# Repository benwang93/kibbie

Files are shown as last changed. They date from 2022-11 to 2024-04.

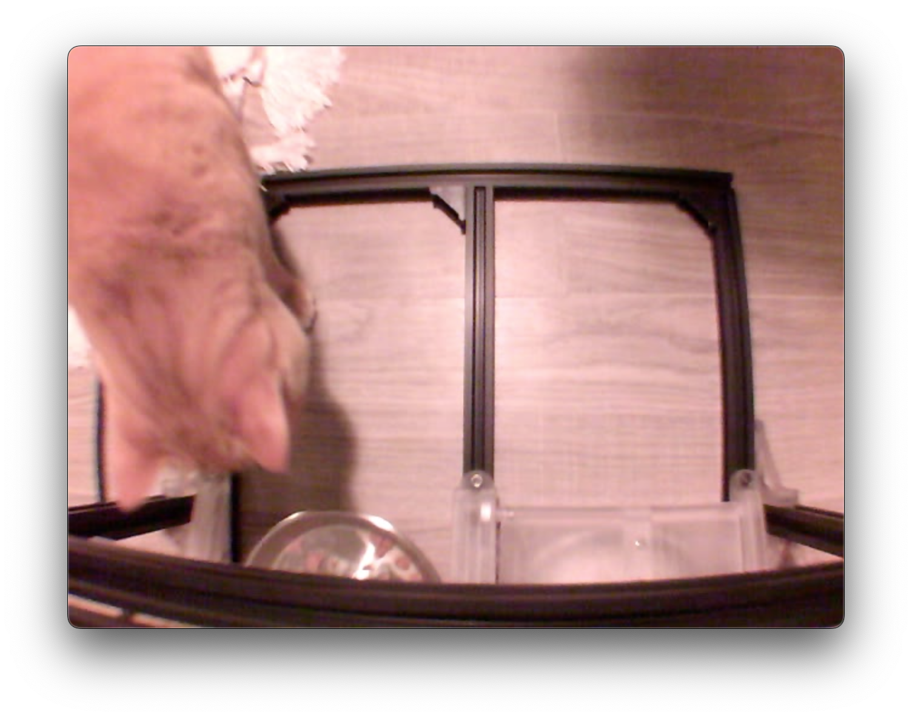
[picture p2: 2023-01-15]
software/images/cami-gray_background.png

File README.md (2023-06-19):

# Project Kibbie

Automated kibble dispenser

## Setup

### Raspberry Pi (embedded)

Hardware requirements:

- Raspberry Pi 3 B+
- 64 GB MicroSD card with Raspbian (see https://www.raspberrypi.com/software/ for installation instructions)

Instructions:

1. On Raspberry Pi with Raspian, clone this repo to `/home/<username>/`
2. Increase swap size from 100MB to something big (2048MB?). See https://peppe8o.com/set-raspberry-pi-swap-memory/
3. Install required python packages by running `setup_raspberrypi.sh`
4. Enable I2C on Pi via the Pi configuration tool. For more information, see https://learn.adafruit.com/adafruits-raspberry-pi-lesson-4-gpio-setup/configuring-i2c
5. Set up kibbie's run.sh to run on startup

Additionally, set up SSH and VNC on the Pi.

#### Python package setup

To install OpenCV on Raspberry Pi 3 Model B+, followed these instructions: https://raspberrypi-guide.github.io/programming/install-opencv and installed it in a virtualenv. Note that these are part of the `setup_raspberrypi.sh` script.

```
. venv/bin/activate

sudo apt-get install build-essential cmake pkg-config libjpeg-dev libtiff5-dev libjasper-dev libpng-dev libavcodec-dev libavformat-dev libswscale-dev libv4l-dev libxvidcore-dev libx264-dev libfontconfig1-dev libcairo2-dev libgdk-pixbuf2.0-dev libpango1.0-dev libgtk2.0-dev libgtk-3-dev libatlas-base-dev gfortran libhdf5-dev libhdf5-serial-dev libhdf5-103 python3-pyqt5 python3-dev -y

pip install opencv-python==4.5.3.56
```

#### Configuring swap memory

Copied from https://peppe8o.com/set-raspberry-pi-swap-memory/ (and tweaked the memory requirement to 2 GB)

Disable swap:

```
sudo dphys-swapfile swapoff
```

Change swap size in dphys-swapfile. Open this file for editing:

```
sudo nano /etc/dphys-swapfile
```

Identify CONF_SWAPSIZE parameter and change according to your needs. For example, I will change it to:

```
CONF_SWAPSIZE=2048
```

Exit and save. Enable swap and restart dphys service:

```
sudo dphys-swapfile swapon
sudo systemctl restart dphys-swapfile.service
```

Check that swap has changed value:

```
pi@raspberrypi:~ $ free
               total        used        free      shared  buff/cache   available
 Mem:         374964       36648      223092        2708      115224      282916
 Swap:        511996           0      511996
```

This will persist also after Raspberry PI reboot.

#### Configuring for run on startup

Source: https://stackoverflow.com/questions/12973777/how-to-run-a-shell-script-at-startup

Set up chrontab for kibbie:

```
$ crontab -e
@reboot  /home/<username>/kibbie/run.sh
```

### PC (development)

Run `setup_desktop.sh` to set up virtualenv and install development packages.

To ignore the `HardwareParameters.py` file, run:

```
git update-index --assume-unchanged software\lib\HardwareParameters.py
```

To start tracking again:

```
git update-index --no-assume-unchanged software\lib\HardwareParameters.py
```

Source: https://stackoverflow.com/questions/23673174/how-to-ignore-new-changes-to-a-tracked-file-with-git

### Software

#### FreeCAD

Design done with FreeCAD 0.20.1. Required modules:

- Assembly 3

##### Assembly 3 installation

1. Tools > Addon Manager
2. Search for and install Assembly 3
3. After restarting FreeCAD, load something that uses Assembly 3 (or select it from the menu, maybe create a new assembly?)
4. Will prompt you to install `py-slvs`. The install will appear to fail, but this is due to pip saying it needs to be upgraded. You're OK to dismiss the repeated prompts to install at this point.
5. Click on an assembly in the Model pane on the left, make sure that the assembly's "Solver Type" is set to "SolveSpace" in the left-hand "Property" pane.

# Feeder servo demo

See the `servo_demo` folder. Parts needed:

- `hardware\prints\servo_mount_plate\servo_mount_plate.ctb`
- `hardware\prints\servo_coupler_v1\Servo_coupler_v1.ctb`

Run script `servo_demo\kibbie_dispenser_demo.py`

## Other info

- [MakerFocus PWM Servo Motor Driver IIC Module 16 Channel PWM Outputs 12 Bit Resolution I2C Compatible with Raspberry Pi 4 3B+ 3B Zero/Zero W/Zero WH and Jetson Nano on Amazon](https://www.amazon.com/gp/product/B07H9ZTWNC)
- [Adafruit I2C configuration guide](https://learn.adafruit.com/adafruits-raspberry-pi-lesson-4-gpio-setup/configuring-i2c)
- [Adafruit Servo Hat instructions](https://learn.adafruit.com/adafruit-16-channel-pwm-servo-hat-for-raspberry-pi/attach-and-test-the-hat)

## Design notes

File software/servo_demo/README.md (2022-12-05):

# Servo demo

2 demos are contained here:
1. Demo from Waveshare (doesn't work very well and I had to change the python library from smbus to smbus2)
2. Adafruit library demo (works very well!)

Notes:
- Commanding angle changes faster than 100ms seems to cause the communication to be unstable and program crashes
- To run, install `adafruit-circuitpython-servokit` and then run `python3 adafruit_lib_test.py`

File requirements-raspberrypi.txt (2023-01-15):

opencv-python==4.5.3.56
adafruit-circuitpython-servokit
matplotlib

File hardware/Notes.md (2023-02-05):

# Design notes

## Servo coupler

### Servo horn

Hole pattern

- Diameter of horn is 20.6mm
- Screw holes
  - 12.80mm is closest between y-axis opposite screw holes
  - Each screw hole is 1.45-1.5mm diameter
  - Designing with 1.45mm for now (making it tighter)
- Distance from horn center to screw hole center on x/y axes must then be
    (12.80 / 2) + 1.45/2 mm = 7.125mm

- Closest measurement between the 2 outer holes in a 3-row is 5.4mm
- So the spacing between 2 holes should be: (5.4mm + 1.45) / 2 = 3.425mm

### D Shaft design & plate thickness

- D shaft is around 5.65mm from flat side of D to the opposite side of circle
  - D shaft diameter is 7.60mm

How long should the shaft be? How thick should base plate be?

- Servo:
  - From screw plate top to top of servo horn is ~16mm
- Hand turn
  - Chrome part sits flush with black plastic when fully inserted
  - Rod is around 64mm long
  - at 39mm from chrome handle, the taper happens on the D shaft

- So from servo horn face to end of rod should be around (64 - 16) = 50mm
- For v1, we can have the screws enter from the far side from the servo and then poke out of the servo horn at the servo side. This would require our base piece to be around 6.5 mm
  - Screw is 10mm long (excluding the tip, which adds around another 1 mm)

Base plate thickness: 6.5mm
Shaft length: 50mm - 6.5mm = 44.5mm

### D Shaft taper

- Last 25mm of shaft is tapered

## Kibbie Monitor Circuit Design

### Design requirements:
- P1: Monitor each dispenser's servo motor current (3 servos per corral, 2 corrals total)
- P1: Communicate overcurrent per-side to Raspberry Pi for shutting down bad side and falling back to single side operation
- P1: Ability to shut off servos on overcurrent. This might be doable via thee Raspberry Pi though?
- P1: Run off of 5V power from PSU
- P2: Watchdog via GPIO, where Raspberry Pi toggles a GPIO while Kibbie program is alive
- P2: Ability to cut power to Raspberry Pi if watchdog sees failure (5V relay, but to Kibbie)

### Components:
- USB A Breakout: https://www.sparkfun.com/products/12700
- Arduino Uno breadboard shield: https://www.sparkfun.com/products/13819
- Current sensor: https://www.sparkfun.com/products/12040
- Current sensor resistor:
  - 0.1 Ohm 5W 10 pcs: https://smile.amazon.com/HUABAN-10PCS-Watts-Metal-Resistor/dp/B08LW2THTJ

### Current monitoring:

#### Selecting R_S
Stall current of each servo is around 3A (https://smile.amazon.com/dp/B07MFK266B). 2 servos active at once (door + door lock) would be 6A.

From the Sparkfun hookup guide:

          V_OUT * 1kOhm
  I_S = ----------------
          R_S * R_L

To not consume too much power on the current sense resistor (so it's not terribly big), we could do:

P = I^2 * R

Let I = 6A. For a max power of 1.5W (so that we could use a 3W resistor), we would need around R = 1.5 W / 6A ^ 2 = 0.0417 Ohms. Can probably round up and use a **0.05 Ohm resistor, 3W**.

#### Selecting R_L

Next is to select a R_L. To get a reasonable voltage reading, let's say max current of 8A (which is what our power supply can do):

            I_S * 1kOhm
  V_OUT = ----------------
            R_S * R_L
            
            I_S * 1kOhm
  R_L = ----------------
            R_S * V_OUT

So at max current:

          8A * 1kOhm
  R_L = ---------------- = 32 kOhm, and a larger R_L would give a lower V_max. So we should be no less than 32 kOhm on R_L
          0.05Ohm * 5V

**Either 33k or 39k Ohm should work.**

#### Final voltages

Using:
            I_S * 1kOhm
  V_OUT = ----------------
            R_S * R_L

and R_S = 0.05 Ohm, R_L = 33 kOhm:

I_S   V_OUT         P_R (W)
0.1	  0.060606061	  0.0005
0.5	  0.303030303	  0.0125
1	    0.606060606	  0.05
1.5	  0.909090909	  0.1125
2	    1.212121212	  0.2
3	    1.818181818	  0.45
4	    2.424242424	  0.8
5	    3.03030303	  1.25
6	    3.636363636	  1.8
7	    4.242424242	  2.45
8	    4.848484848	  3.2

(See hardware/Electrical/Current_sense_calculations.xlsx)

### Reference:
- Current sensor hookup guide: https://learn.sparkfun.com/tutorials/ina169-breakout-board-hookup-guide

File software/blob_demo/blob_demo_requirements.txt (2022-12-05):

opencv-python
adafruit-circuitpython-servokit
matplotlib
scikit-image

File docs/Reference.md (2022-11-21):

Waveshare 16-channel servo driver documentation: https://www.waveshare.com/wiki/Servo_Driver_HAT
Adafruit guide and drivers: https://learn.adafruit.com/adafruit-16-channel-servo-driver-with-raspberry-pi/overview
RPi 3.5" LCD touchscreen documentation: https://www.waveshare.com/wiki/3.5inch_RPi_LCD_(A)

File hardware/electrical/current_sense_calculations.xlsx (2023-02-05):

R_S | 0.05 | Ohm
R_L | 33000 | Ohm
I_S | V_out | P_R
0.1 | 0.06060606061 | 0.0005
0.5 | 0.303030303 | 0.0125
1 | 0.6060606061 | 0.05
1.5 | 0.9090909091 | 0.1125
2 | 1.212121212 | 0.2
3 | 1.818181818 | 0.45
4 | 2.424242424 | 0.8
5 | 3.03030303 | 1.25
6 | 3.636363636 | 1.8
7 | 4.242424242 | 2.45
8 | 4.848484848 | 3.2

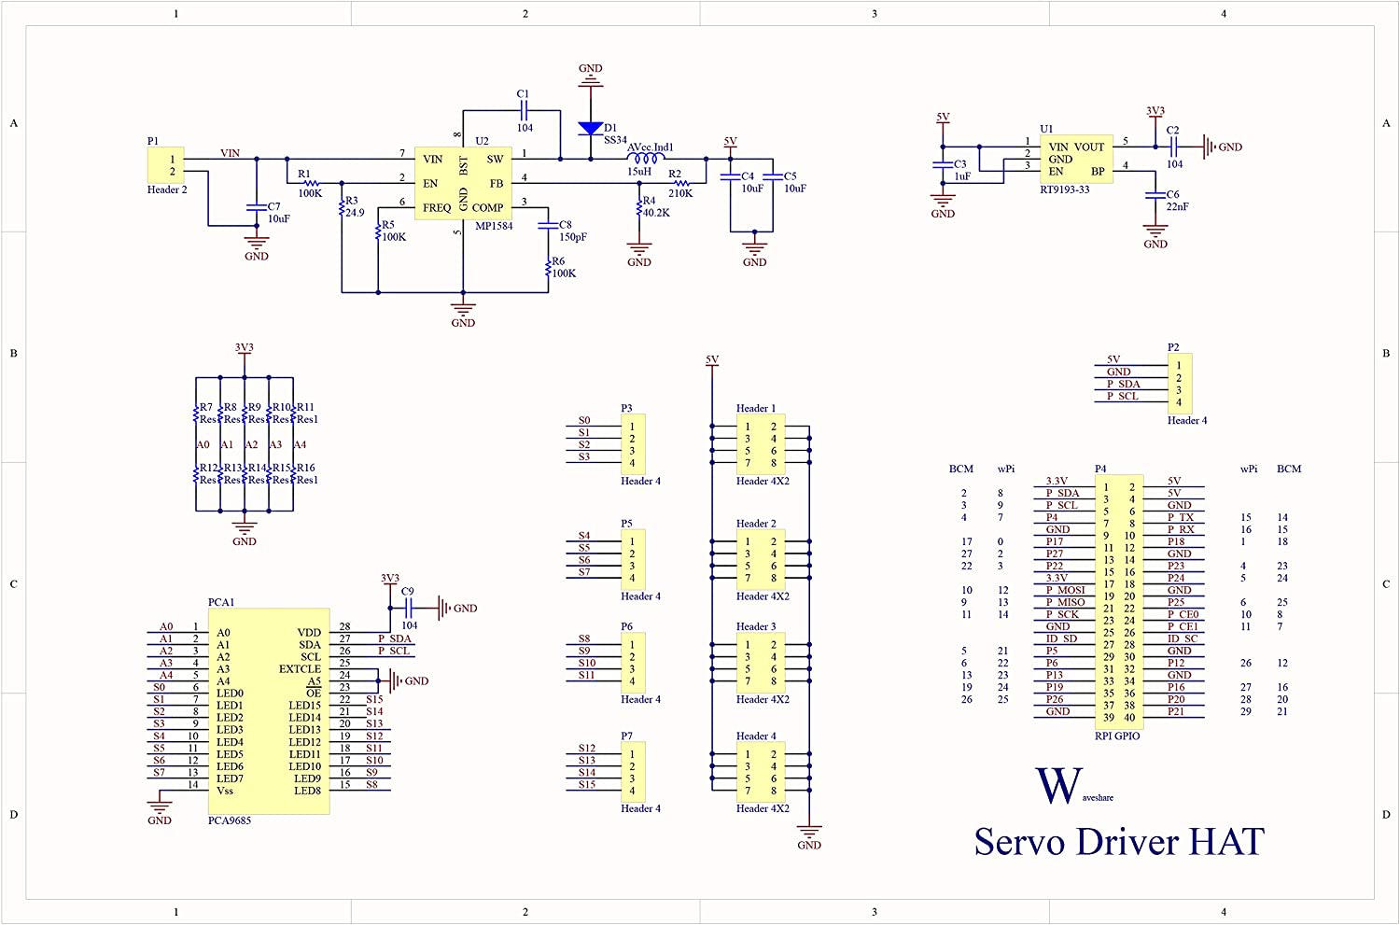
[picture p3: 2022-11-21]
docs/servo_hat_pinout.jpg

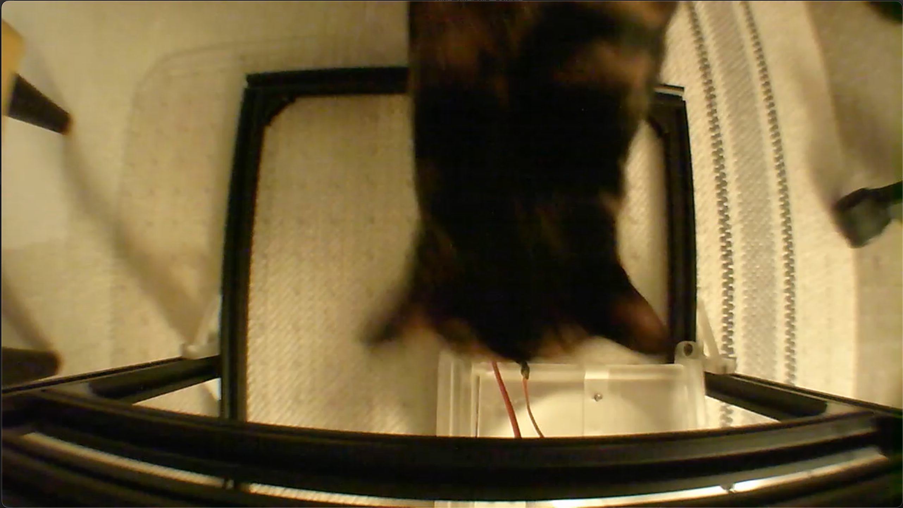
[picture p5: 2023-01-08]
software/images/noodle-white_background.png

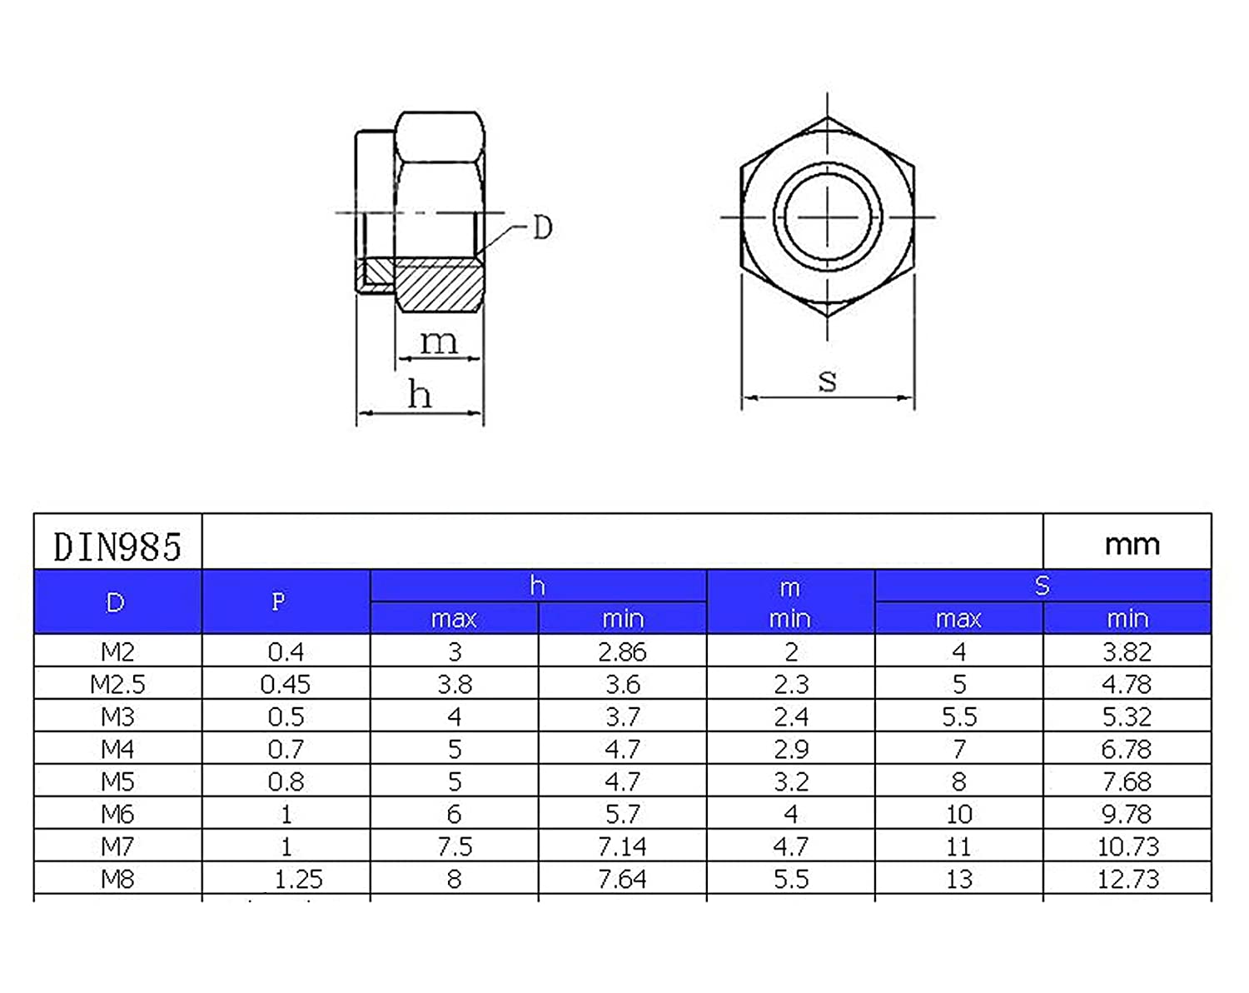
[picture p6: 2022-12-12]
docs/lock_nut_dimensions.jpg

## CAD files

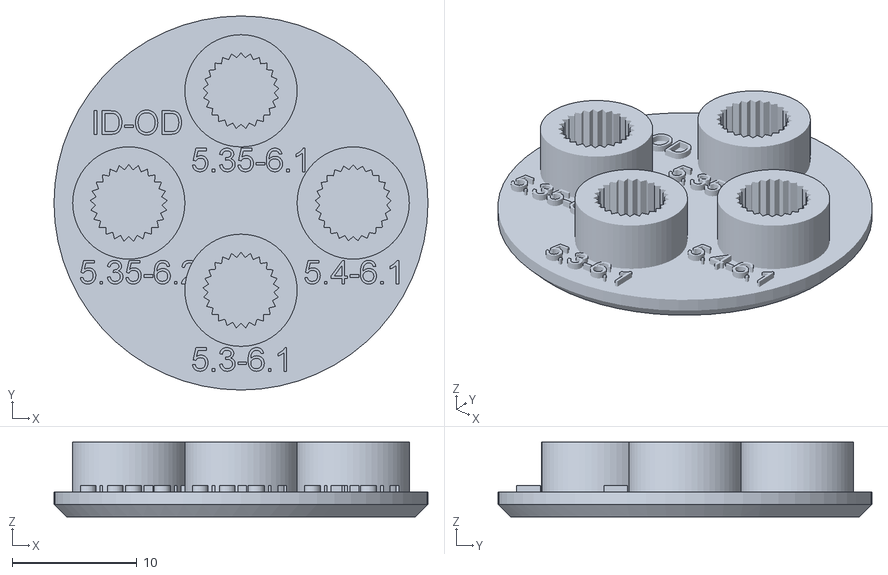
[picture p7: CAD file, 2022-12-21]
hardware/servo_spline_template/test_template_v3_middle-Assembly.stl
30.0 x 30.0 x 6.00

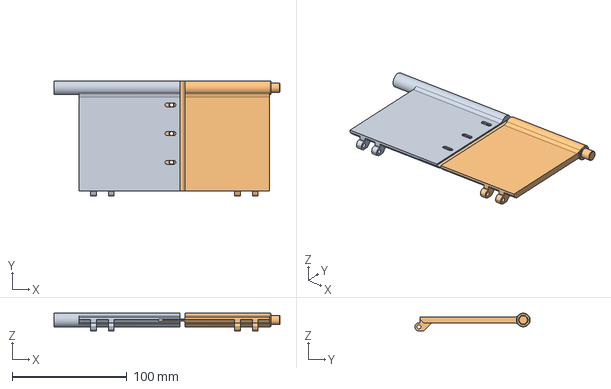
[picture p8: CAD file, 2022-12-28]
hardware/feeder_assembly.FCStd
197.0 x 100.5 x 15.5 mm
Slice006.0
Slice006.2

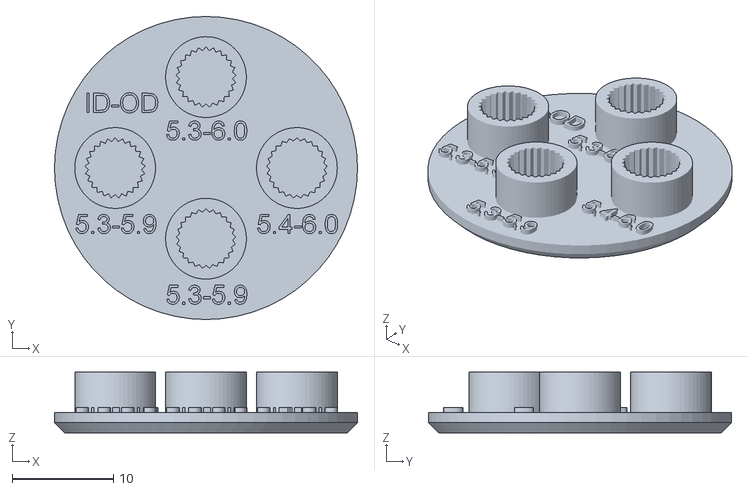
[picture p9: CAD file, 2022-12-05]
hardware/servo_spline_template/servo_test_template-Assembly.stl
30.0 x 30.0 x 6.00

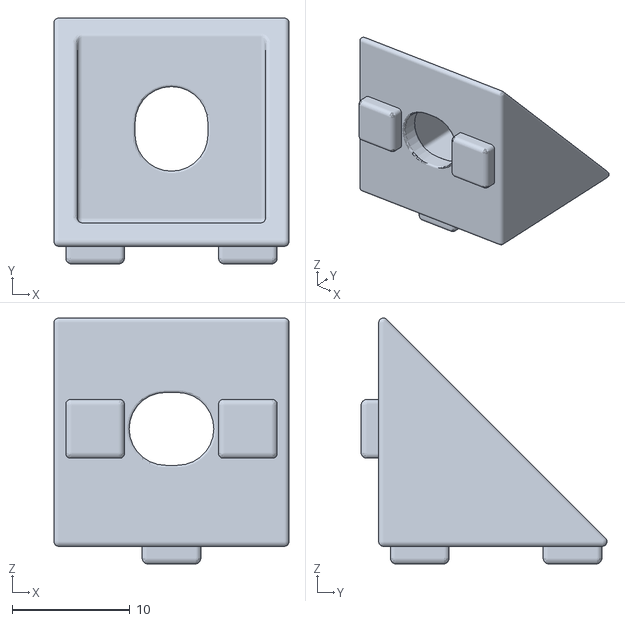
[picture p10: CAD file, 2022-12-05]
hardware/20221128-prints/orthogonal_2020_aluminum_connector-Bodyorthogonal_2020_aluminum_connector.stl
20.0 x 20.9 x 20.9

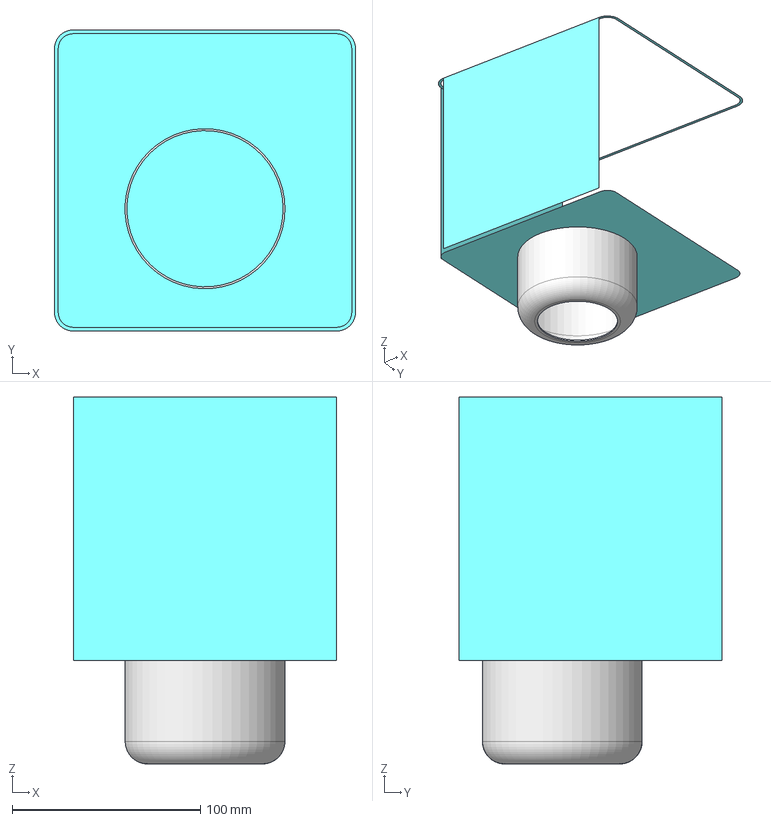
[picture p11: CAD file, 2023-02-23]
hardware/dispenser.FCStd
160.0 x 160.0 x 195.0 mm
FunnelBody
Element
Element001
Element002
Element003

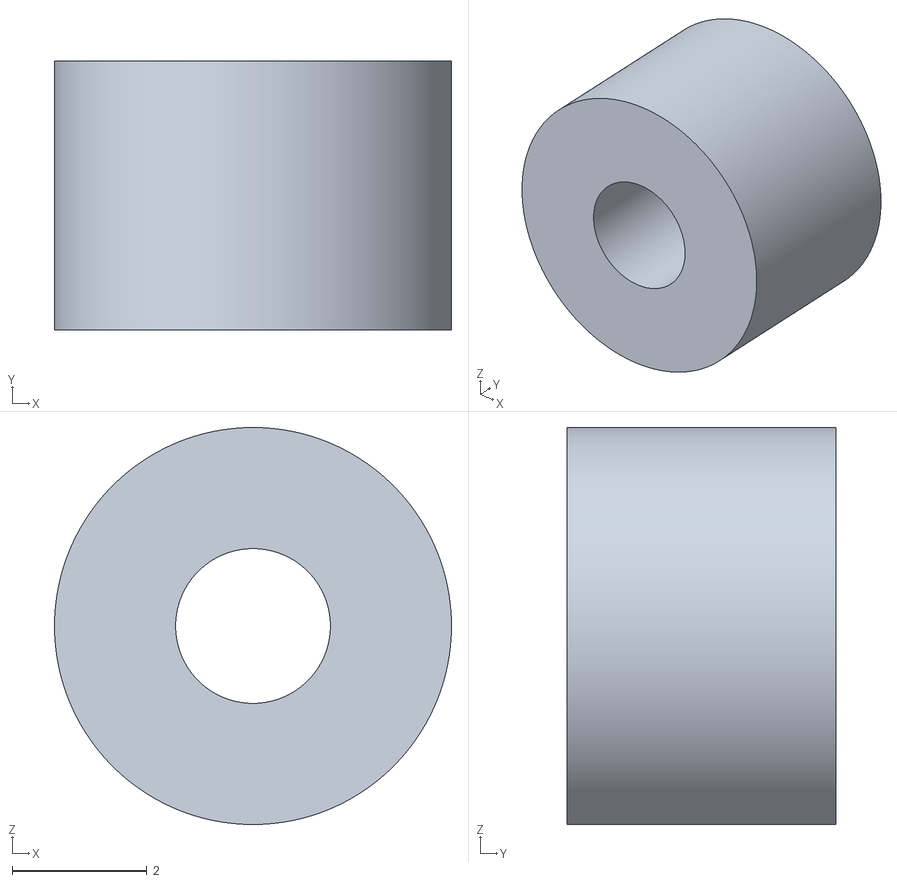
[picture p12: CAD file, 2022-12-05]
hardware/original_MG996R_STL_files/shaft.stl
5.90 x 4.00 x 5.90

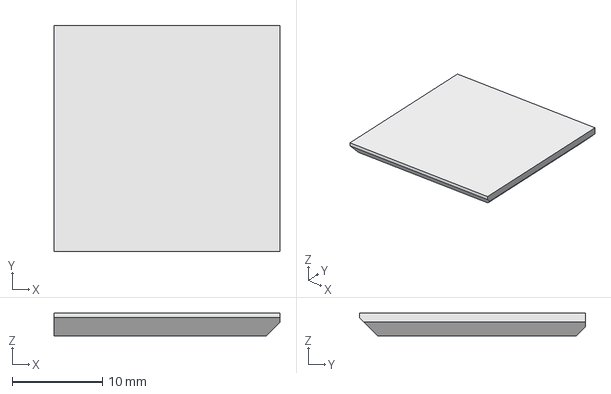
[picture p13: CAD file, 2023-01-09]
hardware/prints/bed_adhesion_test_tile_for_electronics_case/test_tile.FCStd
25.0 x 25.0 x 2.50 mm

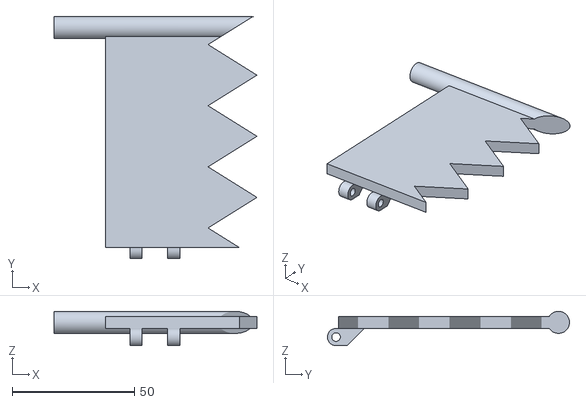
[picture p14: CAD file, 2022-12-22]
hardware/prints/door-left-far-left/door-left-back-far-left.0.stl
83.0 x 99.0 x 14.0

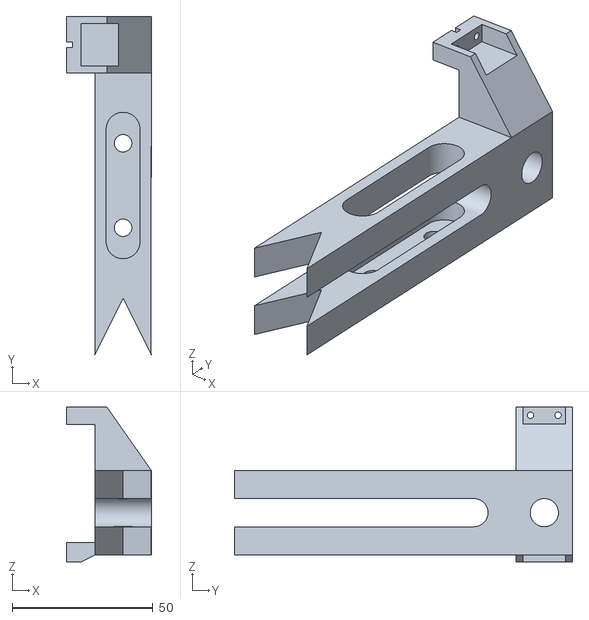
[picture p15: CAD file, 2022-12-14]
hardware/prints/slide-left/slide-left-slice1.stl
30.0 x 120.0 x 55.0

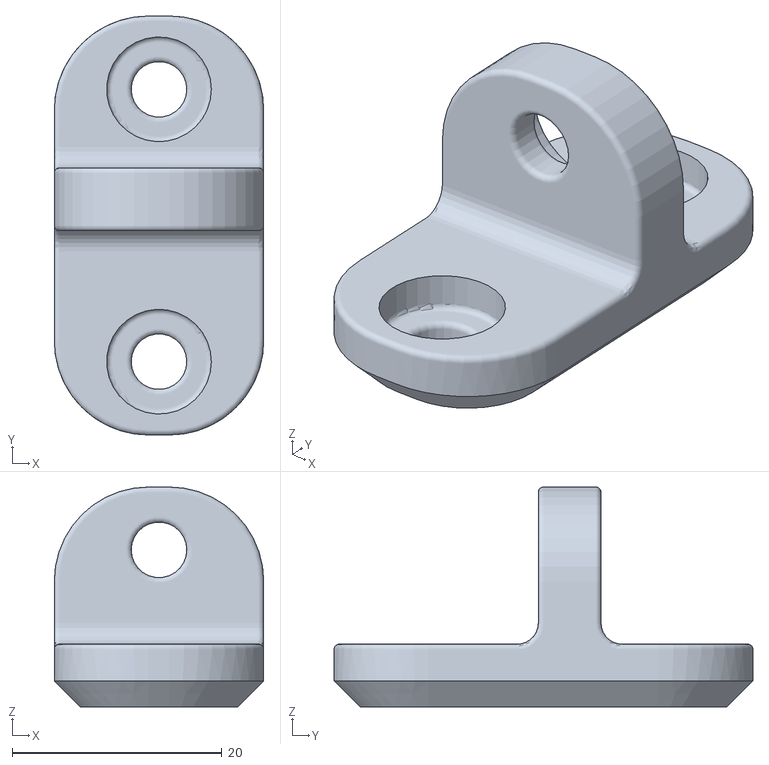
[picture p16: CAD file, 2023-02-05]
hardware/prints/v1-dividers/divider_perpendicular.stl
20.0 x 40.0 x 21.0

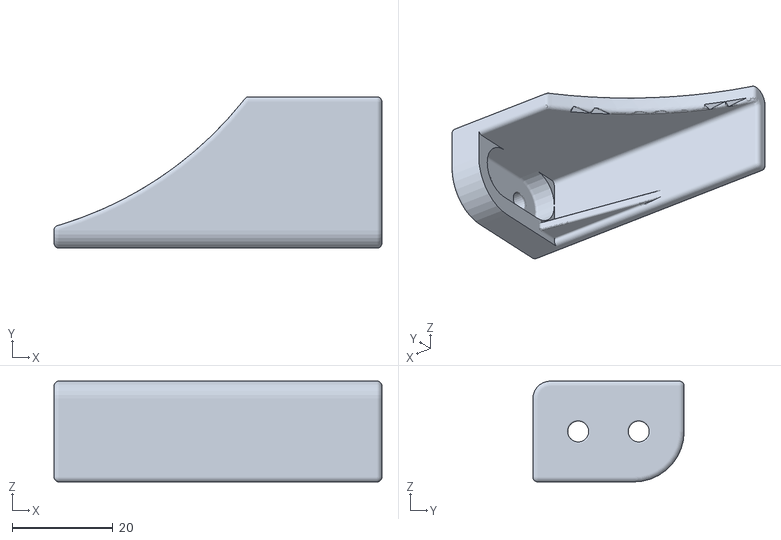
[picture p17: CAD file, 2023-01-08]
hardware/prints/v1_dish_retainers/v1_dish_retainer_FR.stl
65.0 x 30.0 x 20.0

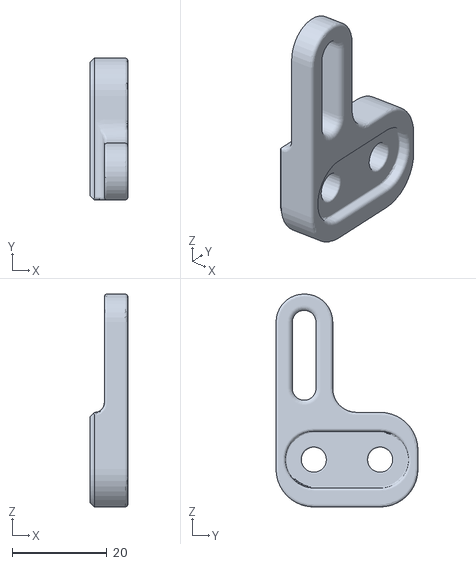
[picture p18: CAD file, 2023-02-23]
hardware/prints/v1_door_crush_support_25mm/25mm_door_crush_support_left.stl
8.00 x 30.0 x 45.0

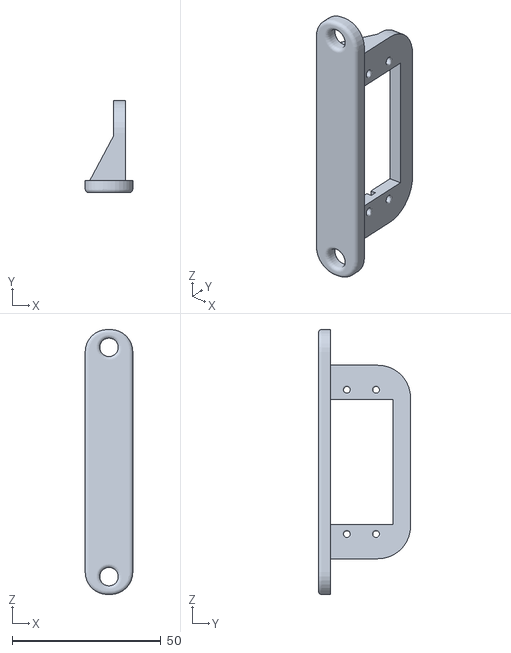
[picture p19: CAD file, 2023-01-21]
hardware/prints/v1_lock_assy_left/v1-lock_servo_mount.stl
16.0 x 31.0 x 89.0

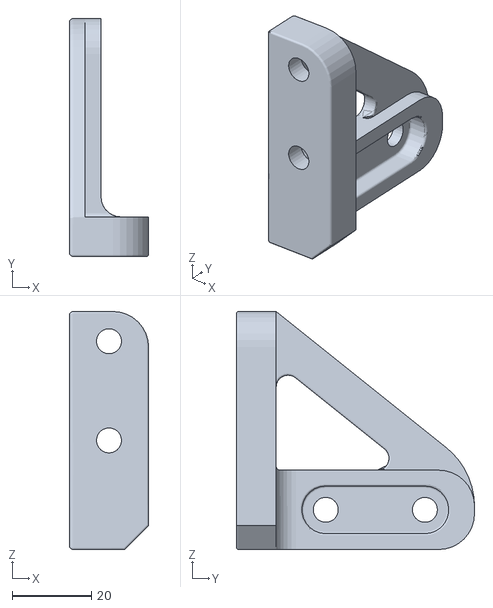
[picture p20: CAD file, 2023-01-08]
hardware/prints/v2_orthogonal_connectors/orthogonal_connector_v2_right.stl
20.0 x 60.0 x 60.0

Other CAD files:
hardware/servo_spline_template/test_template_v2_larger-Assembly.stl
hardware/prints/slide_left_v2_ramp/door-back-left-far-left.stl
hardware/prints/v3.1_left_door_v2.1_left_slide/v3.1_back_door_left.stl
hardware/prints/v3.1_left_front_door_v2_mid_slide/mid_slide_front.stl
hardware/40cm_2020_aluminum_extrusion.FCStd
hardware/MG996R.FCStd
hardware/Servo_coupler_v1.FCStd
hardware/Servo_coupler_v1.stl
hardware/Servo_door_slider-left.FCStd
hardware/food_dish.FCStd
hardware/original_MG996R_STL_files/MG996R.stl
hardware/original_MG996R_STL_files/servo.stl
hardware/orthogonal_2020_aluminum_connector.FCStd
hardware/prints/bed_adhesion_test_tile_for_electronics_case/test_tile.stl
hardware/prints/door-left-far-left/door-left-front-far-left.0.stl
hardware/prints/slide_left_v2_ramp/door-front-left-far-left.stl
hardware/prints/slide_left_v2_ramp/slide-left-slice-back.stl
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

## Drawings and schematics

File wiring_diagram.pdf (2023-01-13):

# Kibbie Wiring Diagram

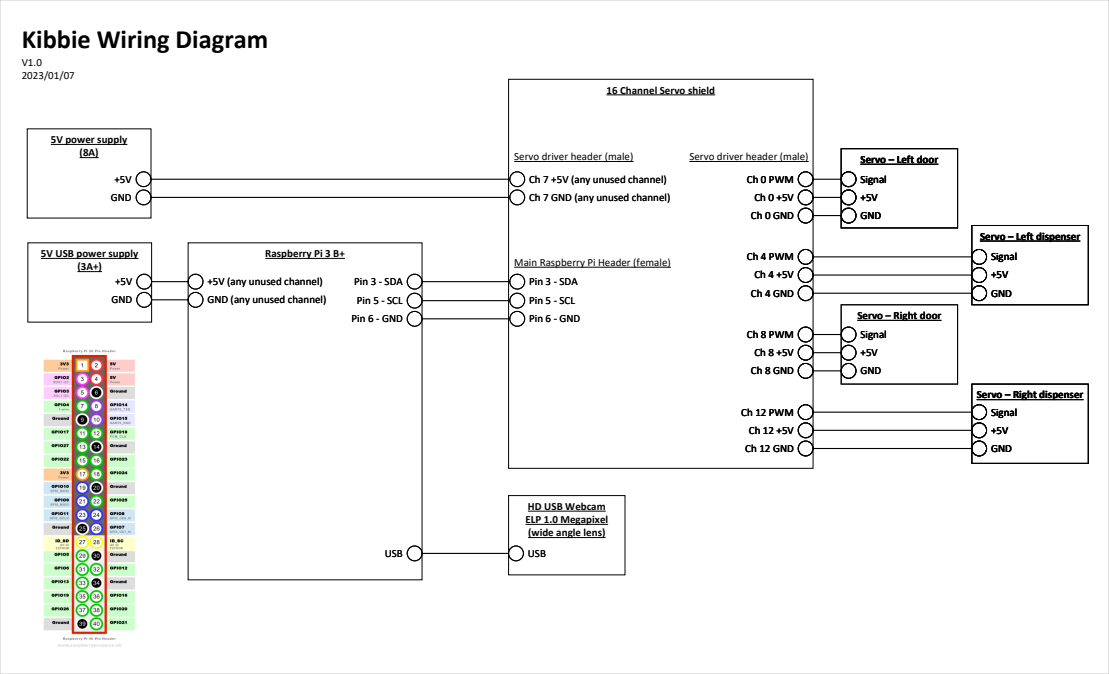
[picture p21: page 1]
5V power supply (8A); Raspberry Pi 3 B+; GND; Pin 3 - SDA; Pin 6 - GND; Pin 5 - SCL; Servo – Right door; Ch 12 PWM; Ch 12 GND; Ch 8 PWM; Ch 8 GND; Ch 4 PWM; Ch 4 GND; Ch 0 PWM; Ch 0 GND; Signal; Servo – Right dispenser; Servo – Left dispenser; Servo – Left door; USB

16 Channel Servo shield

Servo driver header (male)

Ch 7 +5V (any unused channel)
Ch 7 GND (any unused channel)

5V USB power supply

Main Raspberry Pi Header (female)
Pin 3 - SDA
Pin 5 - SCL
Pin 6 - GND

+5V (any unused channel)
GND (any unused channel)

HD USB Webcam
ELP 1.0 Megapixel
(wide angle lens)

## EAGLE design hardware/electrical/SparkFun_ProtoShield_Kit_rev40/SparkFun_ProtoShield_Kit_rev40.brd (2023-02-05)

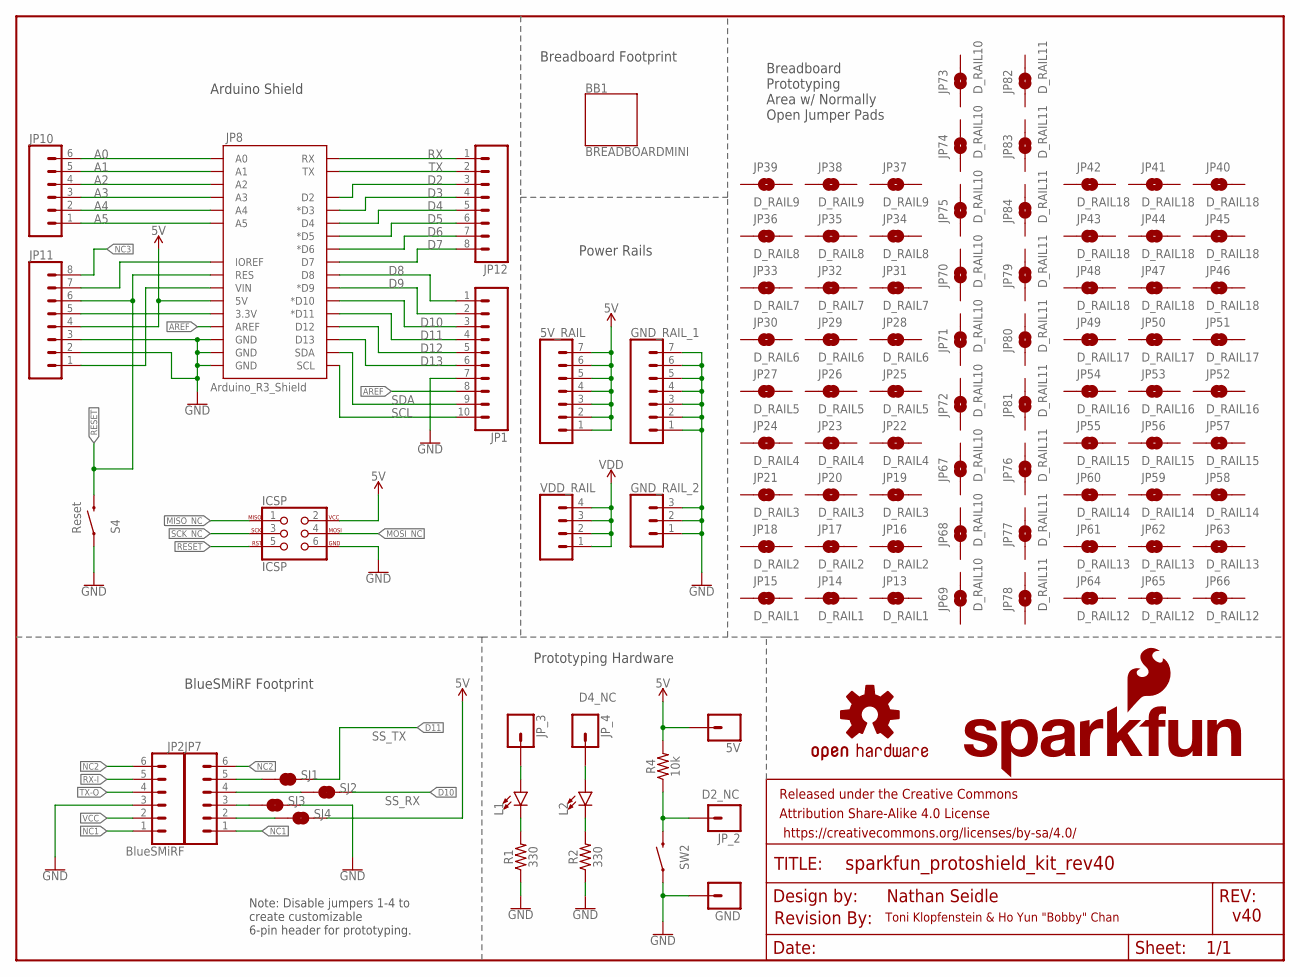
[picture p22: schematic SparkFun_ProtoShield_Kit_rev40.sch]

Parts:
5V: CONN_01; 1X01
5V_RAIL: CONN_07NO_SILK; 1X07_NO_SILK
BB1: BREADBOARDMINI; BREADBOARD-MINI
FRAME1: FRAME-LETTER; CREATIVE_COMMONS
GND: CONN_01; 1X01
GND_RAIL_1: CONN_07NO_SILK; 1X07_NO_SILK
GND_RAIL_2: CONN_031X03_NO_SILK; 1X03_NO_SILK
ICSP: ICSP; 2X3
JP1: CONN_10"; 1X10
JP2: BlueSMiRF; 1X06
JP7, JP10: CONN_06SILK_FEMALE_PTH; 1X06
JP8: ARDUINO_R3_SHIELDR3_PROTO_SHIELD; UNO_R3_PROTO_SHIELD
JP11, JP12: CONN_08"; 1X08
JP13, JP14, JP15: D_RAIL1; SMT-JUMPER_2_NO_NO-SILK
JP16, JP17, JP18: D_RAIL2; SMT-JUMPER_2_NO_NO-SILK
JP19, JP20, JP21: D_RAIL3; SMT-JUMPER_2_NO_NO-SILK
JP22, JP23, JP24: D_RAIL4; SMT-JUMPER_2_NO_NO-SILK
JP25, JP26, JP27: D_RAIL5; SMT-JUMPER_2_NO_NO-SILK
JP28, JP29, JP30: D_RAIL6; SMT-JUMPER_2_NO_NO-SILK
JP31, JP32, JP33: D_RAIL7; SMT-JUMPER_2_NO_NO-SILK
JP34, JP35, JP36: D_RAIL8; SMT-JUMPER_2_NO_NO-SILK
JP37, JP38, JP39: D_RAIL9; SMT-JUMPER_2_NO_NO-SILK
JP40, JP41, JP42, JP43, JP44, JP45, JP46, JP47, JP48: D_RAIL18; SMT-JUMPER_2_NO_NO-SILK
JP49, JP50, JP51: D_RAIL17; SMT-JUMPER_2_NO_NO-SILK
JP52, JP53, JP54: D_RAIL16; SMT-JUMPER_2_NO_NO-SILK
JP55, JP56, JP57: D_RAIL15; SMT-JUMPER_2_NO_NO-SILK
JP58, JP59, JP60: D_RAIL14; SMT-JUMPER_2_NO_NO-SILK
JP61, JP62, JP63: D_RAIL13; SMT-JUMPER_2_NO_NO-SILK
JP64, JP65, JP66: D_RAIL12; SMT-JUMPER_2_NO_NO-SILK
JP67, JP68, JP69, JP70, JP71, JP72, JP73, JP74, JP75: D_RAIL10; SMT-JUMPER_2_NO_NO-SILK
JP76, JP77, JP78, JP79, JP80, JP81, JP82, JP83, JP84: D_RAIL11; SMT-JUMPER_2_NO_NO-SILK
JP_2, JP_3, JP_4: CONN_01; 1X01
L1, L2: LED3MM; LED_3MM
LOGO1: OSHW-LOGOS; OSHW-LOGO-S
R1, R2: 330; AXIAL-0.3
R4: 10k; AXIAL-0.3
S4: MOMENTARY-SWITCH-SPST-PTH-6.0MM; TACTILE_SWITCH_PTH_6.0MM
SJ1, SJ2, SJ3, SJ4: JUMPER-SMT_2_NC_TRACE_SILK; SMT-JUMPER_2_NC_TRACE_SILK
SW2: MOMENTARY-SWITCH-SPST-PTH-6.0MM; TACTILE_SWITCH_PTH_6.0MM
U$1: SFE_LOGO_NAME_FLAME.1_INCH; SFE_LOGO_NAME_FLAME_.1
U$2: REVISION
VDD_RAIL: CONN_041X04_NO_SILK; 1X04_NO_SILK

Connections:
3.3: JP8.3.3V, JP11.5
5V: 5V.1, 5V_RAIL.1, 5V_RAIL.2, 5V_RAIL.3, 5V_RAIL.4, 5V_RAIL.5, 5V_RAIL.6, 5V_RAIL.7, ICSP.2, JP8.5V, JP11.4, R4.P$2 (2), SJ4.2
A1: JP8.A1, JP10.5
A2: JP8.A2, JP10.4
A5: JP8.A5, JP10.1
AREF: JP1.8, JP8.AREF
D2: JP8.D2, JP12.3
D2_NC: JP_2.1, R4.P$1 (1), SW2.3 (2)
D3: JP8.D3 (*D3), JP12.4
D4: JP8.D4, JP12.5
D5: JP8.D5 (*D5), JP12.6
D6: JP8.D6 (*D6), JP12.7
D7: JP8.D7, JP12.8
D8: JP1.1, JP8.D8
D9: JP1.2, JP8.D9 (*D9)
D10: JP1.3, JP8.D10 (*D10), SJ2.2
D11: JP1.4, JP8.D11 (*D11), SJ1.2
D12: JP1.5, JP8.D12
D13: JP1.6, JP8.D13
GND: GND.1, GND_RAIL_1.1, GND_RAIL_1.2, GND_RAIL_1.3, GND_RAIL_1.4, GND_RAIL_1.5, GND_RAIL_1.6, GND_RAIL_1.7, GND_RAIL_2.1, GND_RAIL_2.2, GND_RAIL_2.3, ICSP.6, JP1.7, JP2.3, JP7.3, JP8.GND@0 (GND), JP8.GND@1 (GND), JP8.GND@2 (GND), JP11.2, JP11.3, R1.P$1 (1), R2.P$1 (1), S4.1, SJ3.1, SJ3.2, SW2.1
JP3: JP_3.1, L1.A
JP4: JP_4.1, L2.A
MISO_NC: ICSP.1
MOSI_NC: ICSP.4
unnamed: JP8.IOREF, JP11.7
unnamed: JP8.A0, JP10.6
unnamed: JP8.A4, JP10.2
unnamed: JP8.A3, JP10.3
unnamed: L1.K (C), R1.P$2 (2)
unnamed: L2.K (C), R2.P$2 (2)
NC1: JP2.1, JP7.1
NC2: JP2.6, JP7.6
NC3: JP11.8
RESET: ICSP.5, JP8.RES, JP11.6, S4.3 (2)
RX: JP8.RX, JP12.1
RX-I: JP2.5, JP7.5, SJ1.1
SCK_NC: ICSP.3
SCL: JP1.10, JP8.SCL
SDA: JP1.9, JP8.SDA
TX: JP8.TX, JP12.2
TX-O: JP2.4, JP7.4, SJ2.1
VCC: JP2.2, JP7.2, SJ4.1
VDD: VDD_RAIL.1, VDD_RAIL.2, VDD_RAIL.3, VDD_RAIL.4
VIN: JP8.VIN, JP11.1

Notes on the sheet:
Nathan Seidle
v40
Toni Klopfenstein & Ho Yun "Bobby" Chan
Arduino Shield
Power Rails
Prototyping Hardware
Breadboard Footprint
BlueSMiRF Footprint
Note: Disable jumpers 1-4 to create customizable 6-pin header for prototyping.
Arduino_R3_Shield
Reset
SS_TX
SS_RX
Breadboard Prototyping Area w/ Normally Open Jumper Pads
D4_NC

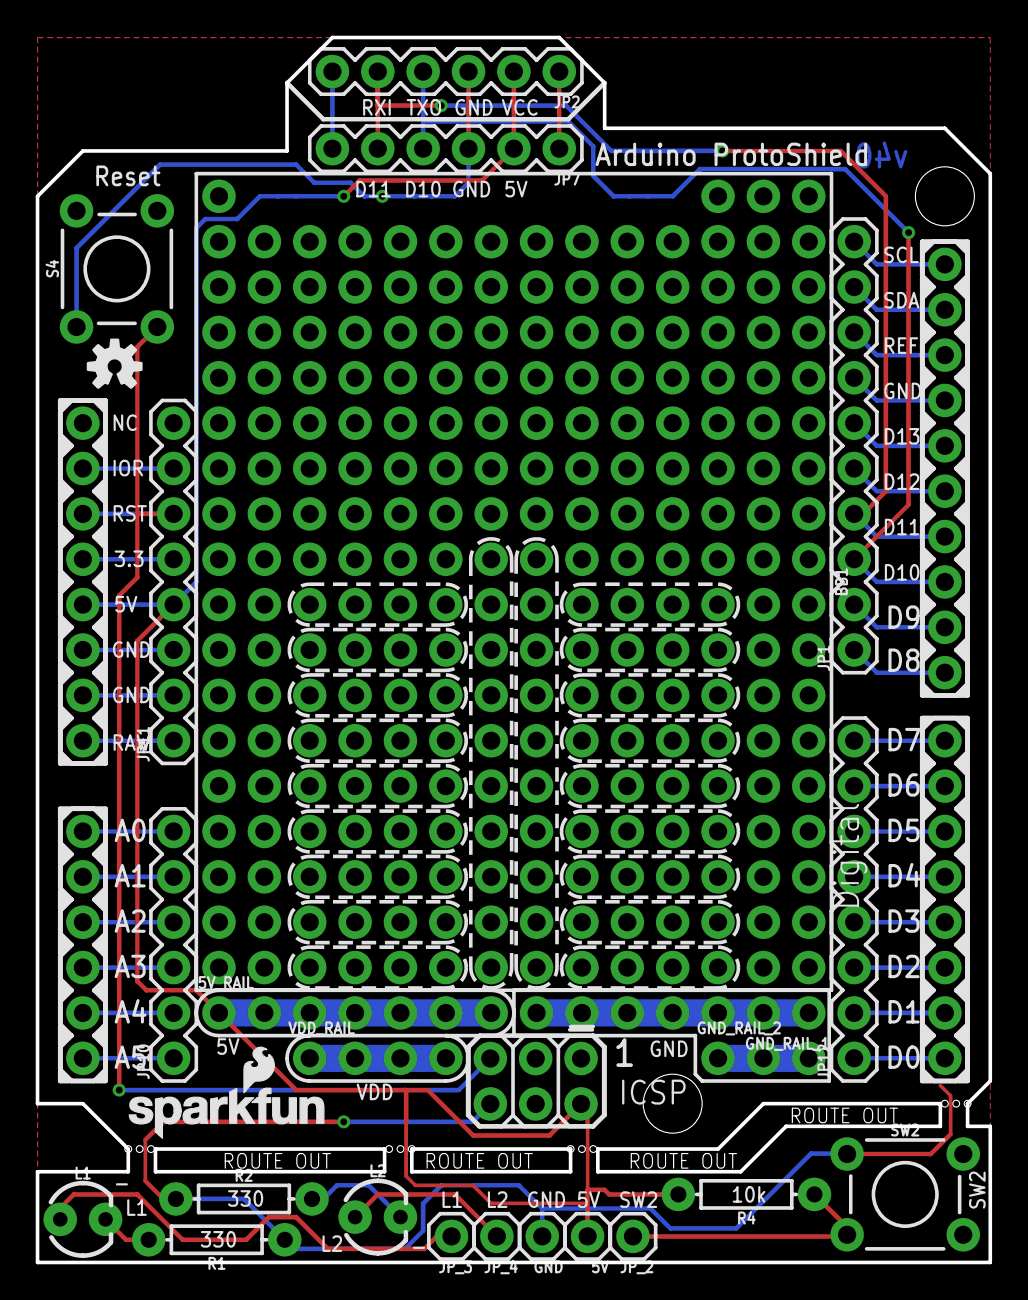
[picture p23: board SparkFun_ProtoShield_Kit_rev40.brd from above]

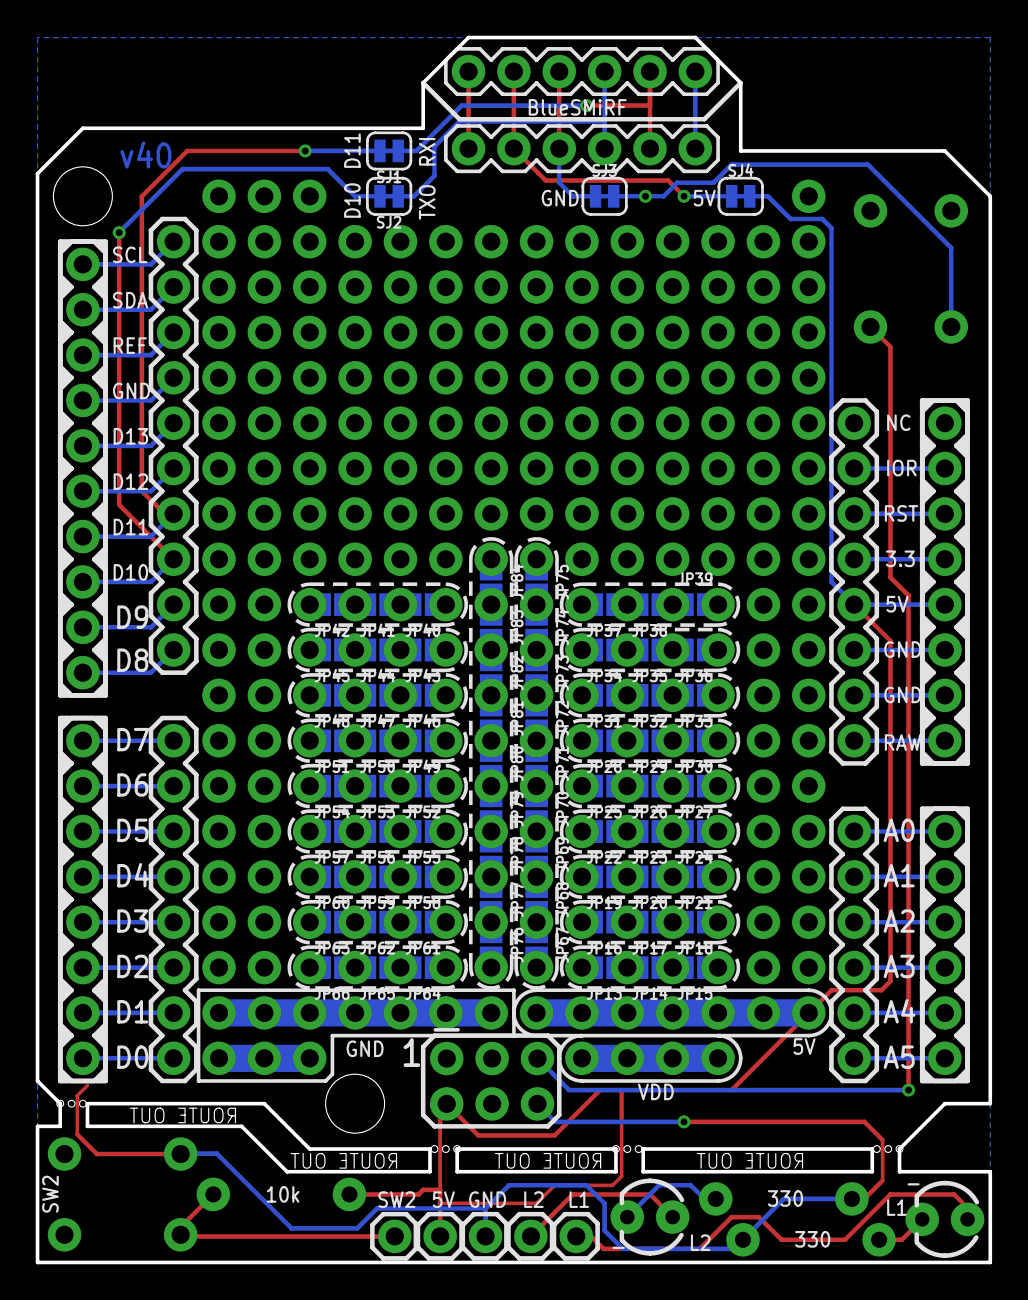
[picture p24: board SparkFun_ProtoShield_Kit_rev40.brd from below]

Board: 2 copper layers, 53.3 x 68.6 mm, 105 parts (76 on the bottom side), 40 nets.

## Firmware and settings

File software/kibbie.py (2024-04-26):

import os
import time
from multiprocessing import Process, Queue

import cv2
import matplotlib.pyplot as plt
import numpy as np

import lib.ImgTools as ImgTools
import lib.KibbieServoUtils as Servo
from lib.Dispenser import Dispenser
from lib.KibbieSerial import KibbieSerial

from lib.Parameters import *

########################
# Constants
########################

# Scale factor applied to the image dimensions to speed up processing
# and get the image to fit on the screen
#
# The results from this script will be scaled back up by this same scale
# so that kibbie.py can scale it back down according to its own scale.
# scale = 0.5 # For quality
# scale = 0.25
scale = 0.1 # For speed

# In addition to processing `scale` used above, scale up the display to this size:
display_scale = 0.25

# Amount of ms to wait after each frame before the next one
# Use this to intentionally slow down frame rate, or use 1 ms for fastest performance
FRAME_PERIOD_MS = 1
# FRAME_PERIOD_MS = 100

# Masks for left and right areas
# Use the "unscaled" coordinates from `camera_calibration.py`
# White background video:
# MASK_REGION_LEFT = [[676.0, 480.0], [680.0, 88.0], [752.0, 14.0], [1006.0, 16.0], [1102.0, 128.0], [1108.0, 372.0], [950.0, 408.0], [946.0, 482.0]] # "Noodle's side"
# MASK_REGION_RIGHT = [[630.0, 478.0], [314.0, 470.0], [312.0, 382.0], [84.0, 370.0], [68.0, 52.0], [630.0, 26.0]]                                    # "Cami's side"
# Gray background video on actual kibbie HW:
MASK_REGION_RIGHT = [[316.0, 378.0], [326.0, 26.0], [18.0, 30.0], [22.0, 286.0], [122.0, 286.0], [140.0, 364.0]]
MASK_REGION_LEFT = [[356.0, 376.0], [350.0, 20.0], [626.0, 22.0], [630.0, 296.0], [550.0, 302.0], [534.0, 372.0]]


# How often the servo process executes
SERVO_PROCESS_PERIOD_S = 0.05 # s, 20 Hz



########################
# Main class
########################
class kibbie:
    # camera: string filepath or int representing video capture device index
    # config: config information, including (per cat):
    #   - Mask polygon (list of [x, y] points describing polygon on UNSCALED image)
    #   - Dispenses per day (float)
    def __init__(self, camera, log_filename, config, servo_command_queue, servo_log_queue) -> None:
        # Open log file (append mode)
        self.logfile = open(log_filename, 'a')
        self.log("=====================================")
        self.log("Initializing kibbie...")

        # Save path to file or index of camera (used to open video capture object)
        self.camera = camera

        # Video capture object
        self.vid = None

        # Store per-cat masks here (mask polygon AND color in range)
        # Resulting white pixels mean that the color matched the cat and in the region of interest
        self.masks = []

        # Track a filtered number of pixels per corral per cat to make door less sensitive
        # Target something like 2s time constant?
        self.filtered_pixels = []
        self.filter_ratio = 0.80 # (every cycle, this fraction of new value will come from previous value)
                                    # Use 0.95 for ~20 FPS
                                    # Use 0.90 for 10 FPS

        # Track door open/close state per corral
        self.corral_door_open = [False for _ in config["corrals"]]

        # Track dispenser state per corral
        self.corral_dispensing = [False for _ in config["corrals"]]

        # Track per-corral dispenser state machines
        self.corral_dispensers = []

        # Preprocess the configuration
        for i,corral in enumerate(config["corrals"]):
            # Pre-scale config values
            print(f'[{corral["name"]}] Before scaling mask: {corral["mask"]}')
            config["corrals"][i]["mask"] = [[int(x[0] * scale), int(x[1] * scale)] for x in corral["mask"]]
            print(f'[{corral["name"]}] After scaling mask: {corral["mask"]}')
            config["corrals"][i]["minPixelThreshold"] = corral["minPixelThreshold"] * scale

            # Initialize mask for each corral
            cat_masks = []
            for _ in config["cats"]:
                cat_masks.append(None)
            self.masks.append(cat_masks)

            # Initialize weighted average number of pixels per cat
            self.filtered_pixels.append([0]*len(config["cats"]))

            # Find farthest left coordinate for debug print
            farthestLeftCoordinate = [99999999999, 0] # Something very far left
            for point in corral["mask"]:
                if point[0] < farthestLeftCoordinate[0]:
                    farthestLeftCoordinate = point
            assert farthestLeftCoordinate != [99999999999, 0], "Could not find farthest left coordinate of mask for debug print"
            config["corrals"][i]["farthestLeftCoordinate"] = farthestLeftCoordinate

            # Initialize dispenser object for each corral
            dispenser = Dispenser(dispenses_per_day=corral["dispensesPerDay"], dispenser_name=corral["name"], logfile=self.logfile)
            self.corral_dispensers.append(dispenser)
        
        self.config = config

        # Placeholder for current scaled frame from camera
        self.images = {}
        self.img = None
        self.hsv_img = None

        # Placeholder for current scaled and quantized frame
        self.quantized = None

        # Timestamp of last frame - used to calculate FPS to display on debug image
        self.last_time_s = None

        # Variables to support periodic frame exports while door is open
        self.export_frame_on_timer = False          # Set to True while door is open to export
        self.next_export_frame_on_timer_time = 0    # Set to next time to export (time.time()) while self.export_frame_on_timer is True

        # Cache dimensions of scaled image
        self.height_px = 0
        self.width_px = 0

        # Variables for tracking state of cats in camera
        self.mask_has_allowed_cat = [False]*Servo.NUM_CHANNELS_USED
        self.mask_has_disallowed_cat = [False]*Servo.NUM_CHANNELS_USED

        # Initialize serial controller (and efuse controller)
        if IS_ARDUINO_MONITOR_ATTACHED:
            self.kbSerial = KibbieSerial()
        else:
            self.kbSerial = None

        # Wait a bit before initializing servos so efuse controller can stabilize
        time.sleep(0.5)

        # Variables for plotting current from serial
        self.current_history = []
        self.fig, self.ax = plt.subplots()

        # Initialize servo controller on a separate process (not hung up by main thread processing)
        # self.servo_command_queue = Queue()      # Kibbie -> Servo queue for commands
        # self.servo_log_queue = Queue()  # Servo -> Kibbie queue for logs to write to disk
        # self.servo_process_handle = Process(target=self.servo_process, args=(self.servo_command_queue, self.servo_log_queue,))
        # self.servo_process_handle.start()
        self.servo_command_queue = servo_command_queue      # Kibbie -> Servo queue for commands
        self.servo_log_queue     = servo_log_queue          # Servo -> Kibbie queue for logs to write to disk

        self.print_help()
    

    def __del__(self):
        self.log("Kibbie shutting down...")
        self.logfile.close()

    #############################################################
    # Servo process methods
    #############################################################
    
    # Helper function to queue servo actions
    def queue_servo_angle_stepped(self, channel, target_angle, latch_channel, latch_angle_unlocked, latch_angle_locked, offset_seconds=0):
        self.servo_command_queue.put(["queue_angle_stepped", channel, target_angle, latch_channel, latch_angle_unlocked, latch_angle_locked, offset_seconds])
    
    def queue_servo_dispense_food(self, channel):
        self.servo_command_queue.put(["dispense_food", channel])
    
    def queue_servo_print_status(self):
        self.servo_command_queue.put(["print_status"])
    
    def queue_servo_exit(self):
        self.servo_command_queue.put(["exit"])
    
    # Periodic function to log servo output to log file
    def process_servo_log_queue(self):
        while not self.servo_log_queue.empty():
            output = self.servo_log_queue.get()
            self.logfile.write(f"{output}\n")
            self.logfile.flush()


    #############################################################
    # Main process methods
    #############################################################

    # Utility to write to the log file and print to console
    def log(self, s):
        output = f"[{time.asctime()}] {s}"
        self.logfile.write(f"{output}\n")
        self.logfile.flush()
        print(output)
    
    # Helper function to scale up images from processing scale to display scale
    def scale_for_display(self, image):
        return cv2.resize(image, (0, 0), fx=display_scale / scale, fy=display_scale / scale)

    # Compute the masks for each corral, where:
    # - Pixel location is within the mask polygon
    # - Pixel color is withtin the HSV filtter for the cat
    def update_cat_masks(self):
        # Generate per-cat masks (intersection of polygon and color filter)
        # For each corral, check for each cat
        for corral_idx,corral in enumerate(self.config["corrals"]):# First filter by polygon
            # Save previous state for transition detection
            prev_allowed = self.mask_has_allowed_cat[corral_idx]
            prev_disallowed = self.mask_has_disallowed_cat[corral_idx]

            # Start with no cats detected
            self.mask_has_allowed_cat[corral_idx] = False
            self.mask_has_disallowed_cat[corral_idx] = False

            for cat_idx,cat in enumerate(self.config["cats"]):
                mask_shape = np.zeros(self.img.shape[0:2], dtype=np.uint8)
                cv2.drawContours(image=mask_shape, contours=[np.array([corral["mask"]])], contourIdx=-1, color=(255, 255, 255), thickness=-1, lineType=cv2.LINE_AA)
                
                # TODO: Iterate over all cats in each region to check for all cats (some operations require 0 or 1 cats)
                # Then filter by cat color
                mask_color = cv2.inRange(self.hsv_img, np.array(cat["lowerHSVThreshold"]), np.array(cat["upperHSVThreshold"]))

                # Combine masks
                self.masks[corral_idx][cat_idx] = cv2.bitwise_and(mask_shape, mask_color)

                # Check for cat
                num_nonzero_px = cv2.countNonZero(self.masks[corral_idx][cat_idx])

                # Perform filter
                num_nonzero_px_filt = (
                    self.filter_ratio * self.filtered_pixels[corral_idx][cat_idx] +
                    (1 - self.filter_ratio) * num_nonzero_px
                )
                self.filtered_pixels[corral_idx][cat_idx] = num_nonzero_px_filt

                # Cat detection logic
                cat_detected = (num_nonzero_px_filt > corral["minPixelThreshold"])
                if cat["name"] in corral["allowedCats"]:
                    cat_is_allowed = True
                    if prev_allowed != cat_detected:
                        self.log(f'Detected allowed cat {cat["name"]} {"entered" if cat_detected else "left"} {corral["name"]} corral')
                    self.mask_has_allowed_cat[corral_idx] |= cat_detected
                else:
                    cat_is_allowed = False
                    if prev_disallowed != cat_detected:
                        self.log(f'Detected disallowed cat {cat["name"]} {"entered" if cat_detected else "left"} {corral["name"]} corral')
                    self.mask_has_disallowed_cat[corral_idx] |= cat_detected

                # Show mask for debug
                debug_mask = self.masks[corral_idx][cat_idx].copy()

                # Make a green (allowed) or red (disallowed) image to display if cat detected
                if cat_detected:
                    if cat_is_allowed:
                        color = (0, 255, 0) # Green
                    else:
                        color = (0, 0, 255) # Red
                    debug_mask_bg = np.zeros(self.img.shape)
                    debug_mask_bg = cv2.rectangle(img=debug_mask_bg, pt1=(0, 0), pt2=(debug_mask_bg.shape[1], debug_mask_bg.shape[0]), color=color, thickness=-1)
                    debug_mask = cv2.bitwise_and(debug_mask_bg, debug_mask_bg, mask=debug_mask)

                # Scale up image for showing
                debug_mask = self.scale_for_display(debug_mask)

                debug_mask = cv2.putText(img=debug_mask, text=f'# pixels: {num_nonzero_px}',
                    org=(5, self.display_height_px - 5), fontFace=cv2.FONT_HERSHEY_SIMPLEX, fontScale=display_scale,
                    color=(255,255,255), thickness=1, lineType=cv2.LINE_AA)
                debug_mask = cv2.putText(img=debug_mask, text=f'# pixels filt: {self.filtered_pixels[corral_idx][cat_idx]:.1f} / {corral["minPixelThreshold"]:.0f}',
                    org=(5, int(self.display_height_px - display_scale * 25 - 5)), fontFace=cv2.FONT_HERSHEY_SIMPLEX, fontScale=display_scale,
                    color=(255,255,255), thickness=1, lineType=cv2.LINE_AA)
                debug_mask = cv2.putText(img=debug_mask, text=f'Detected: {self.mask_has_allowed_cat[corral_idx]}',
                    org=(int(self.display_width_px / 2), self.display_height_px - 5), fontFace=cv2.FONT_HERSHEY_SIMPLEX, fontScale=display_scale,
                    color=(255,255,255), thickness=1, lineType=cv2.LINE_AA)
                win_name = f'mask-{corral["name"]}-{cat["name"]}'
                cv2.imshow(win_name, debug_mask)
                cv2.moveWindow(win_name, (corral_idx + 1) * (self.display_width_px + 50), cat_idx * (self.display_height_px + 25))
                
                # Save images for debug
                self.images[win_name] = debug_mask

    # Check if there are any servo actions to perform
    # Includes door open/close and scheduled dispenser checks
    def check_and_operate_servos(self):
        # Check each region and perform door and dispenser actions
        for i,corral in enumerate(self.config["corrals"]):
            # Check for corral door-open conditions or actively dispensing
            if (self.mask_has_allowed_cat[i] and not self.mask_has_disallowed_cat[i]) or self.corral_dispensers[i].open_door_request:
                if not self.corral_door_open[i]:
                    # Detected a change - log and perform operations
                    self.log(f'Opening {corral["name"]} door')
                    self.queue_servo_angle_stepped(corral["doorServoChannel"], corral["doorServoAngleOpen"], corral["doorLatchServoChannel"], corral["doorLatchServoAngleUnlocked"], corral["doorLatchServoAngleLocked"])
                    
                    self.export_current_frame(postfix=f'opening-{corral["name"]}', annotated_only=True)
                    if self.config["saveSnapshotWhileDoorOpenPeriodSeconds"] > 0:
                        self.export_frame_on_timer = True
                        self.next_export_frame_on_timer_time = (time.time() + self.config["saveSnapshotWhileDoorOpenPeriodSeconds"])
                    
                    self.corral_door_open[i] = True

            else:
                if self.corral_door_open[i]:
                    # Detected a change - log and perform operations
                    self.log(f'Closing {corral["name"]} door')
                    self.queue_servo_angle_stepped(corral["doorServoChannel"], corral["doorServoAngleClosed"], corral["doorLatchServoChannel"], corral["doorLatchServoAngleUnlocked"], corral["doorLatchServoAngleLocked"])

                    self.export_frame_on_timer = False
                    self.export_current_frame(f'closing-{corral["name"]}', annotated_only=True)

                    self.corral_door_open[i] = False
            
            # Check for dispenser commands
            if self.corral_dispensers[i].dispense_request:
                if not self.corral_dispensing[i]:
                    self.corral_dispensing[i] = True

                    self.log(f'Dispensing food in corral {corral["name"]}')

                    # Request dispense once
                    self.queue_servo_dispense_food(corral["dispenserServoChannel"])
            else:
                # Reset flag
                self.corral_dispensing[i] = False
                    

    # Used as part of shut-down sequence
    def close_doors(self):
        for i,corral in enumerate(self.config["corrals"]):
            self.queue_servo_angle_stepped(corral["doorServoChannel"], corral["doorServoAngleClosed"], corral["doorLatchServoChannel"], corral["doorLatchServoAngleUnlocked"], corral["doorLatchServoAngleLocked"])
            self.log(f'Closing {corral["name"]} door')
        
        # self.servo.block_until_servos_done()
        # FIXME: Wait hard-coded time for doors to close until we can get feedback from servo process that doors are all closed
        time.sleep(5.0)
        self.log(f'Doors closed')


    # Used as part of manual servicing sequence
    def open_doors(self):
        for i,corral in enumerate(self.config["corrals"]):
            self.queue_servo_angle_stepped(corral["doorServoChannel"], corral["doorServoAngleOpen"], corral["doorLatchServoChannel"], corral["doorLatchServoAngleUnlocked"], corral["doorLatchServoAngleLocked"])
            self.log(f'Opening {corral["name"]} door')
        
        # We used to block until servos were done moving, but don't have a solution right now after moving servo to its own process
        # self.servo.block_until_servos_done()
        # self.log(f'Doors opened')


    # Presents image and overlays any masks
    def refresh_image(self):
        if self.img is None:
            return
        
        # Draw image
        curr_frame = self.img.copy()

        for i,config in enumerate(self.config["corrals"]):
            # Draw polygon masks
            # Polygon corner points coordinates
            pts = np.array(config["mask"], np.int32)
            pts = pts.reshape((-1, 1, 2))
            
            # Set polygon color based on door open/close state
            if self.corral_door_open[i]:
                color = (0, 255, 0) # Green
            else:
                color = (0, 0, 255) # Red
        
            curr_frame = cv2.polylines(img=curr_frame, pts=[pts], 
                                isClosed=True, color=color, thickness=2)
            
            # For debug print the cat's name over their polygon at the farthest left coordinate
            curr_frame = cv2.putText(img=curr_frame, text=config["allowedCats"][0], org=[config["farthestLeftCoordinate"][0], config["farthestLeftCoordinate"][1] + 20], fontFace=cv2.FONT_HERSHEY_SIMPLEX, fontScale=scale, color=color, thickness=1, lineType=cv2.LINE_AA)
        
        # Scale up image for showing
        curr_frame = self.scale_for_display(curr_frame)

        # Calculate FPS
        curr_time_s = time.time()
        if (curr_time_s - self.last_time_s) > 0:
            fps = 1 / (curr_time_s - self.last_time_s)
        else:
            fps = 0.0
        self.last_time_s = curr_time_s
        curr_frame = cv2.putText(img=curr_frame, text=f"FPS: {fps:.2f}", org=(5, self.display_height_px - 5), fontFace=cv2.FONT_HERSHEY_SIMPLEX, fontScale=display_scale, color=(255,255,255), thickness=1, lineType=cv2.LINE_AA)

        cv2.imshow("raw", self.scale_for_display(self.img))
        cv2.imshow("corrals", curr_frame)

        cv2.moveWindow("raw", 0, 0 * (self.display_height_px + 25))
        cv2.moveWindow("corrals", 0, 1 * (self.display_height_px + 25))

        # Save images for export if needed
        self.images["corrals"] = curr_frame
    

    # Helper function to run the dispenser state machine for each dispenser
    def dispenser_state_machine(self):
        # First see if any cats are in any corrals (don't want to open door if there's a cat nearby)
        any_mask_has_allowed_cat = False
        any_mask_has_disallowed_cat = False
        for i in range(len(self.corral_dispensers)):
            any_mask_has_allowed_cat |= self.mask_has_allowed_cat[i]
            any_mask_has_disallowed_cat |= self.mask_has_disallowed_cat[i]

        # Then update each state machine
        for i,dispenser in enumerate(self.corral_dispensers):
            dispenser.step(any_mask_has_allowed_cat, any_mask_has_disallowed_cat)
    

    # Helper function to export current frame to the `software/images/` folder
    def export_current_frame(self, postfix="", annotated_only=False):
        current_time = time.localtime(time.time())
        filename = time.strftime("%Y-%m-%d_%H-%M-%S", current_time)
        date_string = time.strftime("%Y-%m-%d", current_time)
        
        if postfix != "":
            filename += "-" + postfix
        
        if annotated_only:
            # Single frame export (intended for auto-export)
            folder = f"snapshots/{date_string}"
            os.makedirs(folder, exist_ok=True)

            # Only export the annotated frame of corrals
            cv2.imwrite(f"{folder}/{filename}.png", self.images["corrals"])

            self.log(f'Exported current frame to "f{folder}/{filename}.png"')
        else:
            # Export all frames (intended for user request)
            folder = f"snapshots/{filename}/"
            os.makedirs(folder, exist_ok=True)

            for key in self.images:
                cv2.imwrite(f"{folder}/{key}.png", self.images[key])
            
            self.plot_current(f"{folder}/current.png")

            self.log(f'Exported current frame to "{folder}/*.png"')
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

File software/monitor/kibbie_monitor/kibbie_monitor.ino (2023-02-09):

/*
 * Kibbie watchdog monitor
 * 
 * The Arduino watchdog monitor performs the following tasks:
 *  - Monitors current to each door of Kibbie (door and latch servos combined)
 *  - Reports overcurrent conditions to the Raspberry Pi once timing threshold exceeded
 *  - Monitors digital heartbeat signal from Raspberry Pi that should be toggled while the Kibbie program is running
 *  - If timeout is exceeded, reboot the Raspberry pi via a relay control
 */

// Calibration
const unsigned long OVERCURRENT_THRESHOLD_MS = 5000; // Number of milliseconds of overcurrent allowed before setting the overcurrent output pin high

// Current sense pins
int currentSenseLeftPin = A0;
int currentSenseRightPin = A1;
int overcurrentLeftPin = D4;
int overcurrentRightPin = D5;

// Heartbeat pins
int heartbeatPin = D2;
int mainPowerRelayPin = D3

// Current sense variables
int currentSenseLeftValue = 0;    // variable to store the value coming from the sensor
int currentSenseRightValue = 0;   // variable to store the value coming from the sensor

bool overcurrentActiveLeft = false;   // true if currently overcurrent
bool overcurrentActiveRight = false;  // true if currently overcurrent

unsigned long overcurrentStartTimeLeft = 0;    // milliseconds when the overcurrent condition started
unsigned long overcurrentStartTimeRight = 0;   // milliseconds when the overcurrent condition started


void setup() {
  pinMode(heartbeatPin, INPUT);
  pinMode(mainPowerRelayPin, OUTPUT);
  pinMode(overcurrentLeftPin, OUTPUT);
  pinMode(overcurrentRightPin, OUTPUT);

  // Set initial output state
  digitalWrite(overcurrentLeftPin, LOW);
  digitalWrite(overcurrentRightPin, LOW);
}

void loop() {
  // Read current sensor values
  currentSenseLeftValue = analogRead(currentSenseLeftPin);
  currentSenseRightValue = analogRead(currentSenseRightPin);

  // Track if overcurrent occurs
  // TODO: Do we need a filter? Not sure how noisy this signal will be
  if (currentSenseLeftValue > overcurrentThreshold) {
    // Check for edge
    if (overcurrentActiveLeft) {
      // Check for us exceeding overcurrent time
      if ((millis() - overcurrentStartTimeLeft) > OVERCURRENT_THRESHOLD_MS) {
        print("*** Overcurrent detected on left door for xxx ms");
        digitalWrite(overcurrentLeftPin, HIGH);
      }
    } else {
      // Start of overcurrent. Save overcurrent start time
      overcurrentStartTimeLeft = millis();
      overcurrentActiveLeft = true;
    }
  } else {
    // Clear overcurrent condition
    overcurrentActiveLeft = false;
    digitalWrite(overcurrentLeftPin, LOW);
  }

  // Read heartbeat value
  int heartbeatValue = digitalRead(heartbeatPin);


  // turn the ledPin on
  digitalWrite(ledPin, HIGH);
  // stop the program for <sensorValue> milliseconds:
  delay(sensorValue);

  // turn the ledPin off:
  digitalWrite(ledPin, LOW);
  // stop the program for for <sensorValue> milliseconds:
  delay(sensorValue);
}

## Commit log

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2022-11-26 Add orthogonal 2020 aluminum connector part and to assembly
    [feeder_assembly.FCStd, food_dish.FCStd, orthogonal_2020_aluminum_connector.FCStd]
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2022-11-27 WIP working on sliding door. 2 separate assembly attempts (in main assy and Servo_door_slider-left)
    [MG996R.FCStd, Servo_door_slider-left.FCStd, feeder_assembly.FCStd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]
2022-11-27 WIP sliding door. Add pivot to back door and mid slider blank
    [MG996R.FCStd, Servo_door_slider-left.FCStd, feeder_assembly.FCStd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]
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2022-12-04 Add servo coupler test print + v1 of servo coupler (holes are a bit small and came out lopsided when printed)
    [basic_spline.FCStd, servo_test_template-Assembly.stl, test_template.FCStd]
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2022-12-04 v2 of server mount plate (bigger holes, moved holes north, bigger slot for servo, wider pins for servo
    [servo_mount_plate.FCStd, servo_mount_plate.stl]
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2022-12-06 Add FreeCAD setup instructions and work on door CAD
    [dispenser.FCStd, feeder_assembly.FCStd]
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2022-12-07 Added 2nd set of doors by linking to right set
    [dispenser.FCStd, feeder_assembly.FCStd]
2022-12-10 Disable alignment constraints for the middle and right slider to fix unsolvable constraints
    [feeder_assembly.FCStd]
2022-12-11 WIP redoing all constraints. Using workplanes in assy3 this time
    [dispenser.FCStd, feeder_assembly.FCStd]
2022-12-11 Most constraints there now. also mirrored the doors
    [dispenser.FCStd, feeder_assembly.FCStd]
2022-12-11 Duplicate left slide to make mid slide. convert servo to body (but haven't added it)
    [dispenser.FCStd, feeder_assembly.FCStd]
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2022-12-12 Finished left slide servo mount (not tested yet)
    [dispenser.FCStd, feeder_assembly.FCStd]
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2022-12-12 Add fillets to door hinges and shorten slider mid
    [dispenser.FCStd, feeder_assembly.FCStd]
2022-12-12 Add top slot to left slide to save material. need to drill mounting holes too
    [dispenser.FCStd, feeder_assembly.FCStd, orthogonal_2020_aluminum_connector.FCStd]
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2022-12-13 Add slot for servo cantilever support in left slide
    [dispenser.FCStd, feeder_assembly.FCStd]
2022-12-13 Fix corrupted orthogonal 2020 aluminum connector by restoring from f242ef278fd0c2cc742ffeec2b18b87d9ebdf5ed
    [orthogonal_2020_aluminum_connector.FCStd]
2022-12-13 Fix constraints (right door surfaces got mismatched)
    [feeder_assembly.FCStd]
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2022-12-14 Slice left back door and add STL for slide left part 1
    [dispenser.FCStd, feeder_assembly.FCStd, slide-left-slice1.stl]
2022-12-20 Add v2 (larger) version of servo spline template because v1 cracked at largest size
    [basic_spline.FCStd, servo_test_template-Assembly.stl, test_template.FCStd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]
2022-12-21 Add v3 (middle) version of servo spline template to see if there's a better fit than 5.4-6.2
    [test_template_v3_middle-Assembly.stl, test_template_v3_middle.FCStd]
2022-12-22 Fix spline for back left door and also slice front left door for far-left slice
    [dispenser.FCStd, door-left-back-far-left.0.stl, door-left-front-far-left.0.stl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]
2022-12-22 POORLY split doors into triples. Need to fix front left door constraint (after initial print!)
    [dispenser.FCStd, feeder_assembly.FCStd]
2022-12-24 WIP Adding angled left slide guide. before any bevels
    [dispenser.FCStd, feeder_assembly.FCStd]
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2022-12-24 Add bearing slot and end mounting hole for left slide (ramp version)
    [dispenser.FCStd, feeder_assembly.FCStd]
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2022-12-24 increase spline size, add bearing shaft + retaining hole
    [dispenser.FCStd, feeder_assembly.FCStd]
2022-12-24 WIP adding middle support, but everything seems broken with left slide ramp (can't create chamfers)
    [dispenser.FCStd, feeder_assembly.FCStd]
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2022-12-25 v2 print of left slider (ramp) + door (bearing support)
    [dispenser.FCStd, door-back-left-far-left.stl, door-front-left-far-left.stl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]
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2022-12-26 Fix front left door bearing retaining hole not going all the way through
    [feeder_assembly.FCStd]
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2022-12-27 Some v3 slide/door improvements
    - Shave off 1mm for servo bushing thickness
    - Rename some left slide part design actions for clearer labeling
    - Increase left slide hole from 10mm to 13 for thicker axle
    - Increase length of rear door shaft by 1mm for better servo mating (plus allowing for small gap in rear)
    [dispenser.FCStd, feeder_assembly.FCStd]
2022-12-27 v3 support/front-door related improvements
    - Shorten front door shaft by 5mm
    - Add vertical brace for midpoint of left slide
    [feeder_assembly.FCStd]
2022-12-28 WIP added inial v3 slotted slicer for doors
    [dispenser.FCStd, feeder_assembly.FCStd]
2022-12-28 v3 back left door slicer + neck down - Added v3 slicer to back left door - Neck down back door inside to fit bearing
    [feeder_assembly.FCStd]
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2022-12-28 Back door fillets + more slot length - Add fillets to back door - Expand slots from 5mm to 6mm, with 4mm shortening and 2mm lengthening
    [dispenser.FCStd, feeder_assembly.FCStd]
2022-12-28 WIP v2 slide-mid - WIP Adding v2 slide-mid - Add access hole for 3rd left slide mount hole - Add sketch for slide mid bearing slot, but don't know how to hollow out a part
    [dispenser.FCStd, feeder_assembly.FCStd]
2022-12-28 v3 slicer improvement attempt, but chamfer/fillet issues - WIP Adding shaft portion to slicer so it's not just joined by a thin layer - Added new shaft features to fillet/chamfered parts, couldn't fi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
    [dispenser.FCStd, feeder_assembly.FCStd]
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2022-12-28 v3.1 print (split and slice left back door and left slide)
    [v2.1_left_slide_front.stl, v2.1_left_slide_rear.stl, v3.1_back_door_left.stl]
2022-12-29 WIP v2 mid slide
    - Expand slide-mid to encompass full bearing slot
    - Add bearing slot and mid-support
    [dispenser.FCStd]
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2022-12-29 WIP adding slicer to front door and changing shaft thickness
    [dispenser.FCStd]
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2022-12-30 WIP adding bearing retainer on front door right side - Add bearing retainer on front door right side - Add M3 x 20mm screw
    [dispenser.FCStd]
2022-12-30 v3.1 front door and v2 slide
    - Add fillets to parts
    - Make left front door right side printable (add drainage hole and slant)
    - Added assembly to realign front left door with coordinate system
    - Add sliced parts
    [dispenser.FCStd, food_dish.FCStd, front_door-left-aligned.stl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]
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2023-01-07 Simulate wrong cat at feeder; add print of cat Name on polygons
    [kibbie.py]
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2023-01-08 Split up electronics housing between base and cover. WIP
    [dispenser.FCStd]
2023-01-09 WIP electronics housing
    - Add power jack model, roughly position in assembly
    - Add walls to both base and cover
    [dispenser.FCStd]
2023-01-09 WIP electronics housing
    - Add mounting holes/ standoffs for servo hat and Pi
    - Fixed constraints
    - Add 12mm M3 screw for reference
    - Add sockets in servo hat standoff for M3 lock nuts
    [dispenser.FCStd]
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2023-01-09 Add jack cutouts and attachment points to connect cover/base
    [dispenser.FCStd]
2023-01-09 Add cooling holes/slots and chamfers/fillets to electronic housing
    [dispenser.FCStd]
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2023-01-09 test priunts for 50pct burn in for case
    [test_tile.FCStd, test_tile.stl]
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2023-01-13 Added v2 servo mount plate and prints for fixed front right inside door + v2 servo plate + v1 servo coupler
    [Servo_coupler_v1.stl, servo_mount_plate_v2.FCStd, servo_mount_plate_v2.stl]
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2023-01-15 Fix green mask dimensions
    [kibbie.py]
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2023-01-16 Fix servos blocking indefinitely on startup. Split out/disable servo debug
2023-01-16 Add pause function and ability to interact via basic keyboard shortcuts
    [kibbie.py]
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2023-01-17 Add export feature and fix wrong threshold for Cami's side
    [kibbie.py]
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2023-01-20 Reset flags from desktop dev back to kibbie Raspberry Pi
    [kibbie.py]
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2023-01-21 Add v1 servo lock mount and arm CAD + print
    [dispenser.FCStd, v1-lock_servo_arm.stl, v1-lock_servo_mount.stl]
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2023-01-23 Fix right door latch locked angle calibration
2023-01-23 Give latch servos some tolerance (otherwise chatter while locked)
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2023-01-28 Fix constraints on divider brackets and add left bottom/top
    [dispenser.FCStd]
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2023-02-05 Update servo demo and utils for 3 degree overshoot. Load dispenser angle from persistence
    [servo_angle_commander.py]
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2023-02-14 Add nut retainers to left slide servo mount. Still need to add cantilever reinforcements and integrated paw-walls
    [dispenser.FCStd]
2023-02-14 Add cantilever reinforcements to servo mount
    [dispenser.FCStd]
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2023-02-18 Update current sense sketch to shortened opcode format
    [current_sense_demo.ino]
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2023-02-19 Add plotting of current (though might be memory leaking?)
    [kibbie.py, plot_current.py]
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2023-02-19 Add v4 slide and door prints, however want reinforcements for slide in 4.1
    [left_slide_v4_front.stl]
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2023-02-25 Fix syntax error and disable thread for now (not working, look into multiprocessing next)
    [kibbie.py]
2023-02-26 WIP trying to move servo to its own process, but failing to start right now
    [kibbie.py]
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2023-02-27 Fix typo for queue_servo_dispense_food
    [kibbie.py]
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2023-05-01 Add latch servo overshoot logic
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2024-04-26 Update dispense schedule and swap Noodle's motor
    [kibbie.py]

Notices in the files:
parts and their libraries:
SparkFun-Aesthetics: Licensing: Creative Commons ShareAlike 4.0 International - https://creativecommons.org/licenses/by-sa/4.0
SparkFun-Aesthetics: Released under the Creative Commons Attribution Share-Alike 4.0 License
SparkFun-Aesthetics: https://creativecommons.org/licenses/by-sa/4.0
